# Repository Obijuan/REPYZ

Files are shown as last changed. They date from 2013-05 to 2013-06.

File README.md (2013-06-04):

REPYZ
=====

3D Printable modules for building modular robots

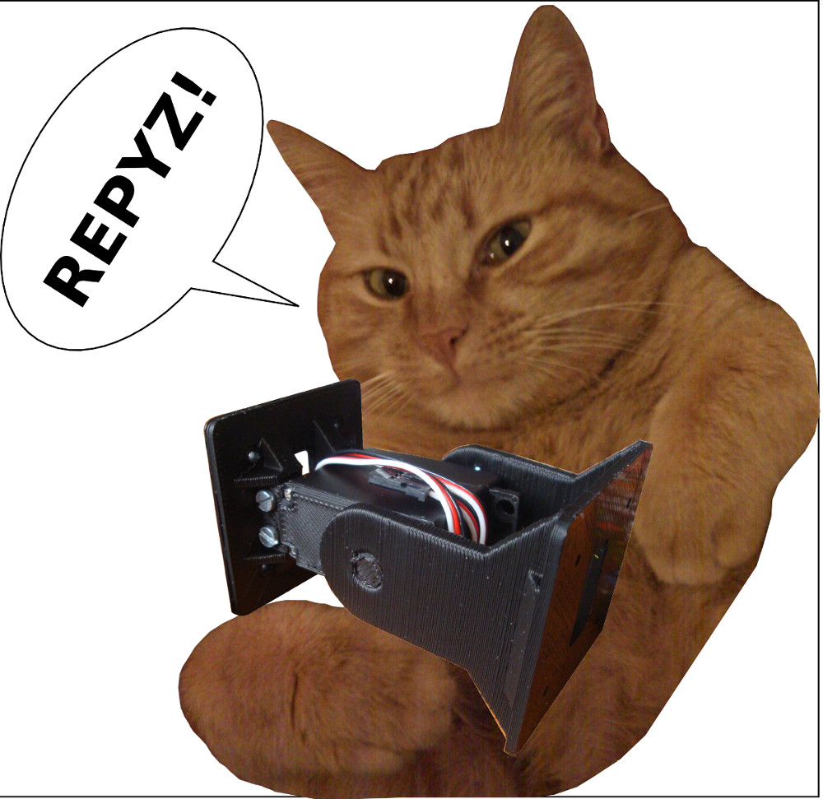
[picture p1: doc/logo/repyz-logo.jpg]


Introduction
--
REPYZ modules are an evolution of the REPY modules. The new fetures are:

- Simplified structure.  The body is smaller than in previous versions, thanks to the new sevo lower cover, with a fake shaft

- More robust and compact

- It is simmetric (like REPY v2). The caterpillar robots can move face up or face down

- PRO Version. There are two flavors of repyz modules: standar and PRO. The later includes a 608 bearing on the fake shaft for making the rotation very smooth and with no clearance.

More information can be found on this link (in Spanish):

http://www.iearobotics.com/wiki/index.php?title=M%C3%B3dulos_REPYZ

Pictures
--

https://plus.google.com/u/0/photos/109138697406392447933/albums/5878857037837654529

Video
--

  An example of the locomotion of a pith-pitch minimal configuration, composed of two repyz modules (standar version). Video presented by my little daughter Alicia :-)

http://www.youtube.com/watch?v=hIY0V6fK7iY

Bill of materials
--

- The 3 printed parts: body, head and servo lower cover (There are two differents heads, one for the standard and the other for the PRO)

- Servo Futaba 3003
- 1 M8 washer
- 1 608 bearing (optional, only for the pro version)
- 4 M3 nuts
- 4 M3x10mm bolts
- 2 M2x12mm bolts (provided with the servo)

Instructions
--



Assembly process:

https://plus.google.com/u/0/photos/109138697406392447933/albums/5884847018420290209

Electronics
--

  For moving the module all types of electronics can be used. The only requirement is the generation of a PWM signal.

  Examples of electronics:

- Arduino
- Skymega board: http://www.thingiverse.com/thing:14197
   -This is the board I am using because it fits perfectly on the REPYZ module
   
Software
--

  For generating the locomotion of snake robots, I am using sinusoidal generators. More information can be found on my phd dissertation:

http://www.iearobotics.com/wiki/index.php?title=Juan_Gonzalez:PhD_Thesis

   I have implemented the ardusnake library (for arduino and arudino compatible boards). It is very simple to use and understand:

  https://github.com/Obijuan/ArduSnake

  http://www.thingiverse.com/thing:21401

Links to other modules
--

- **Y1 modules**: http://www.iearobotics.com/wiki/index.php?title=M%C3%B3dulos_Y1
- **MY1 modules**: http://www.iearobotics.com/wiki/index.php?title=M%C3%B3dulos_MY
- **REPY v1**: http://www.thingiverse.com/thing:688
- **REPY v1.1**: http://www.thingiverse.com/thing:13442
- **REPY v2**: http://www.dsquaredrobotics.com/wiki/index.php?title=REPY-2.0

Author
--

- Juan Gonzalez-Gomez (Obijuan)

Credits
--

- **David Estevez**:  Is the author of the Repy modules v2. Repyz were inspired in Repy v2:
    http://www.dsquaredrobotics.com/wiki/index.php?title=REPY-2.0

- **Andres Prieto-Moreno**. Is the author of the MY1 modules, in which the repyz are also inspired. He also suggested me the idea of including a lower servo cover with ears for the servos. Because of these ears, the body of the module has been dramatically simplified.

- **Gocha** is the cat of Carlos Garcia Saura. It is the one that appears on the REPYZ logo

License
--

REPYZ modules are released under the GPL license

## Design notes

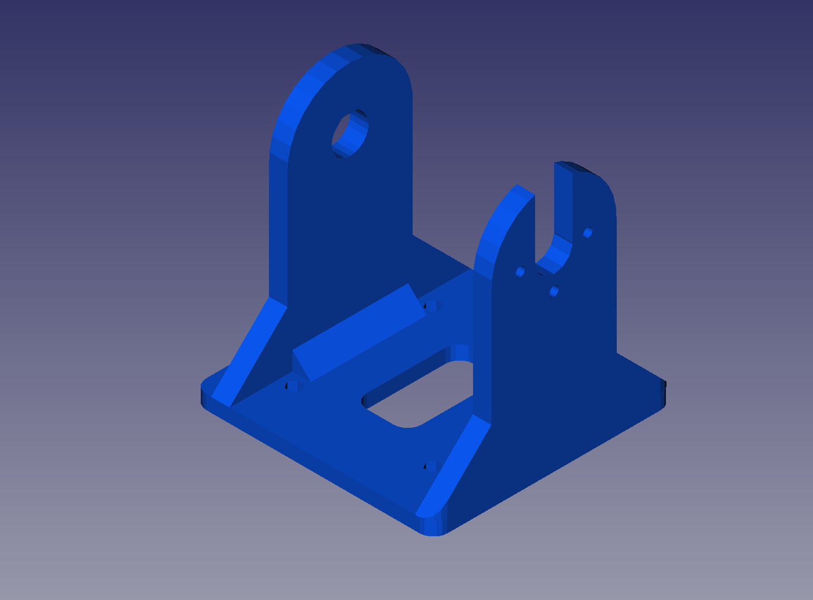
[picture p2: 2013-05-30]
pictures/REPYZ-head.png

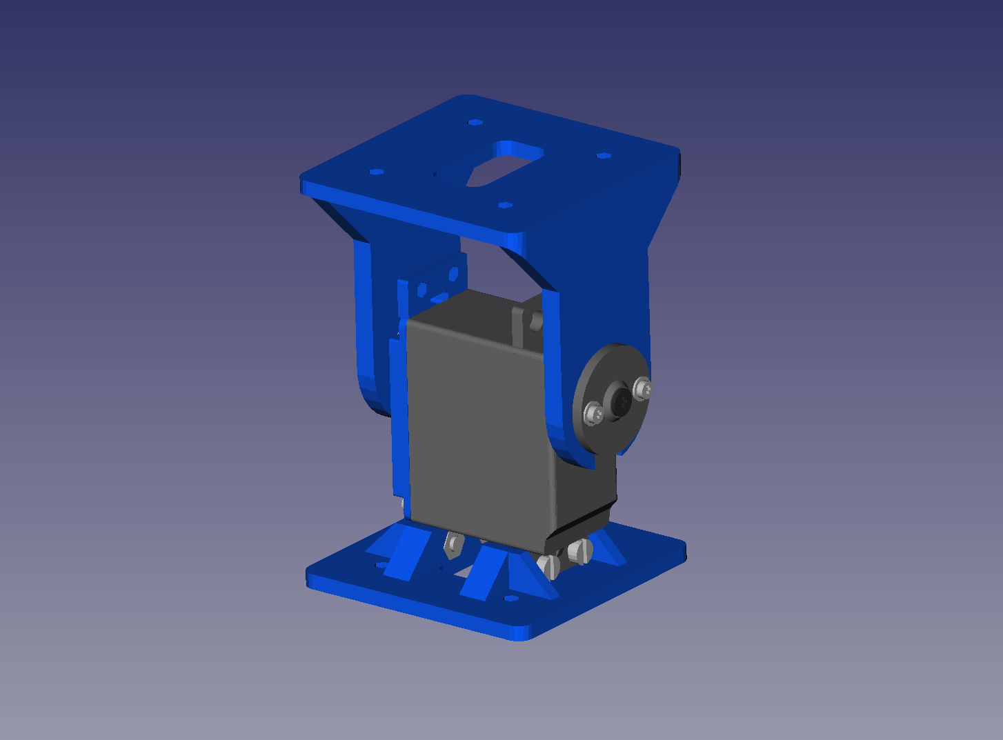
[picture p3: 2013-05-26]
pictures/repyz-module-freecad-1.png

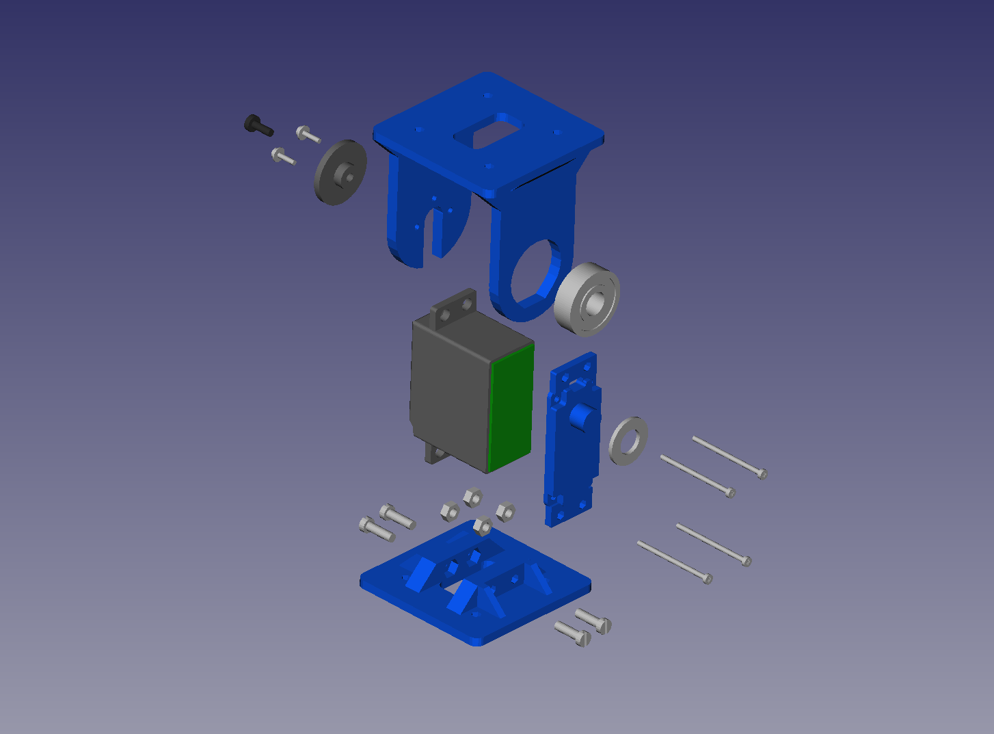
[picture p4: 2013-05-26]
pictures/repyz-PRO-module-exploded-view.png

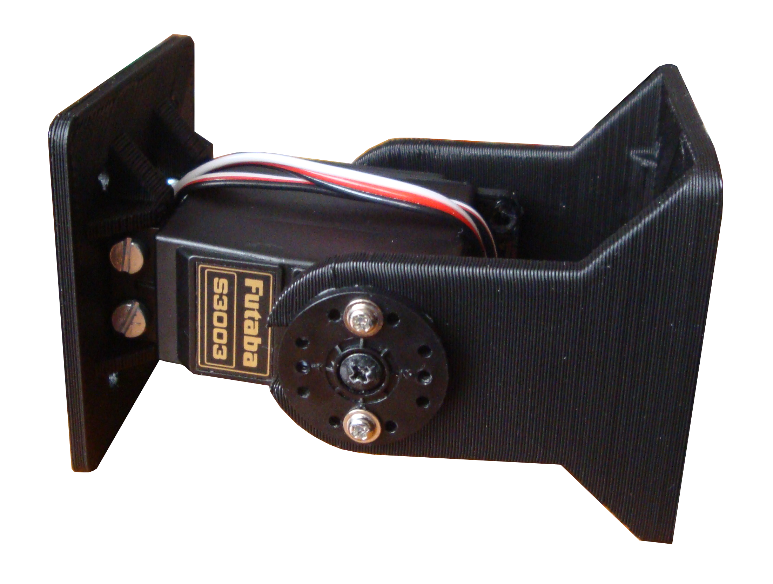
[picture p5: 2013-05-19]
pictures/REPYZ-2.png

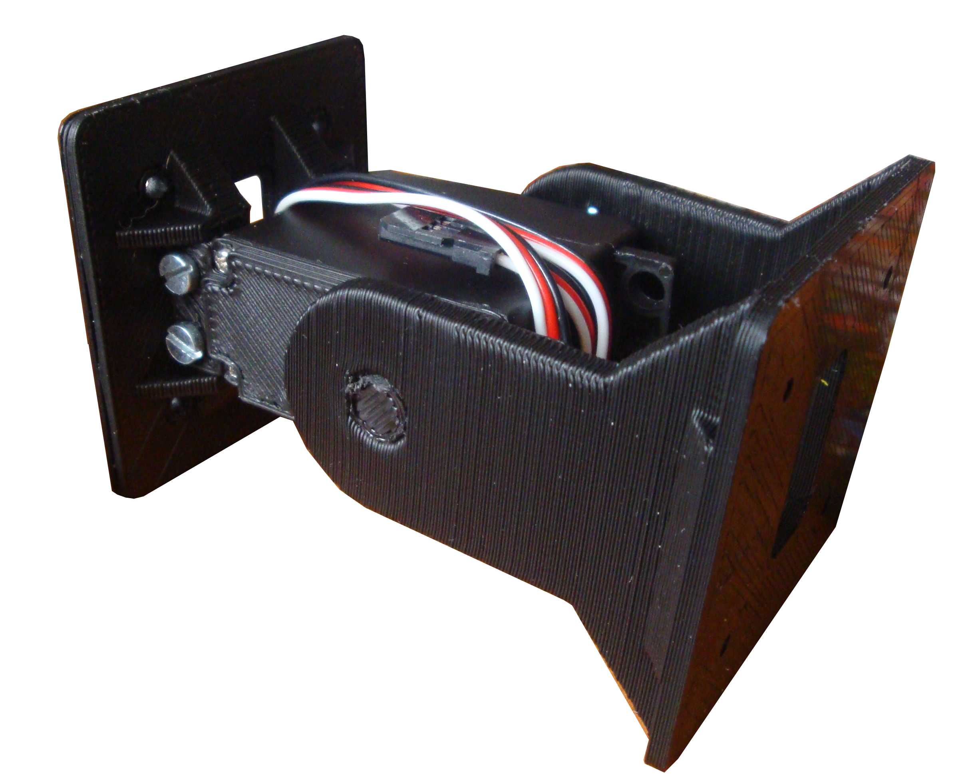
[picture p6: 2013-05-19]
pictures/REPYZ-1.png

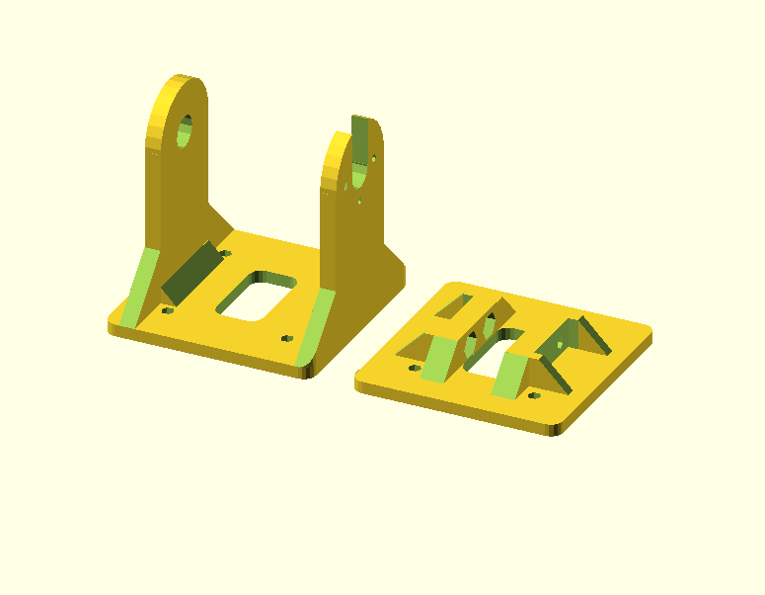
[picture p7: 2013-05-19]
pictures/repyz-body-head-openscad1.png

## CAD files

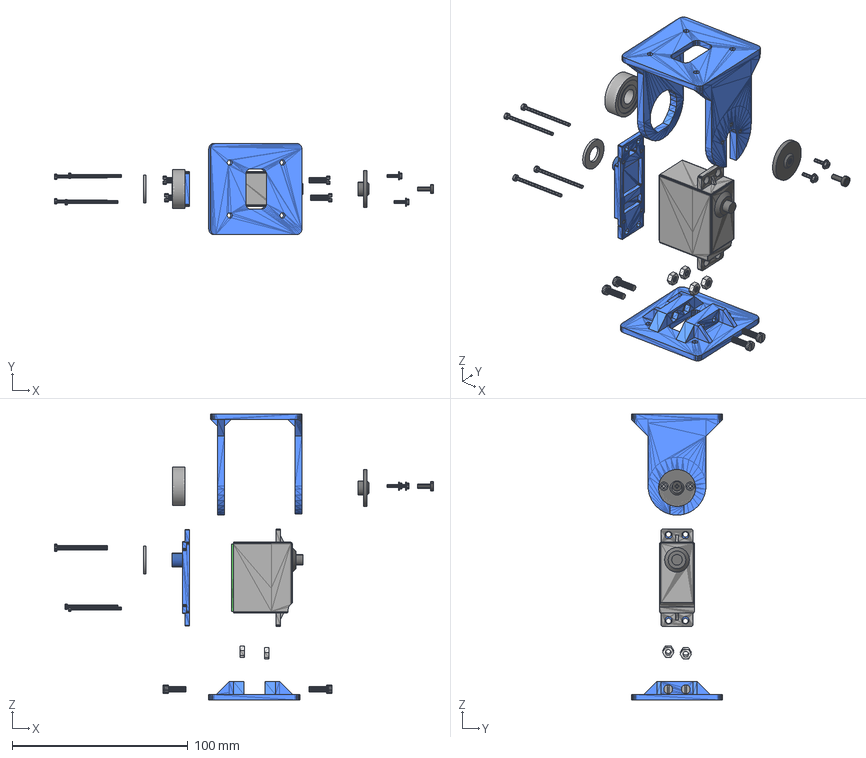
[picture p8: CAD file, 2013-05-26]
doc/Freecad/repyz-PRO-exploded-view.fcstd
215.5 x 52.0 x 162.5 mm
futaba_witout_lower_cover001
futaba_fake_electronics001
servo_lower_cover_ears_shaft001
servo_screw001
servo_screw004
servo_screw005
servo_screw006
repyz-body
nut_M3001
nut_M3004
nut_M3005
nut_M3006
bolt_M3x10_1
bolt_M3x10004
bolt_M3x10005
bolt_M3x10006
washer_M8001
futaba_rounded_horn001
servo_screw2003
servo_screw2004
servo_shaft_screw001
repyz_head_PRO001
bearing_608

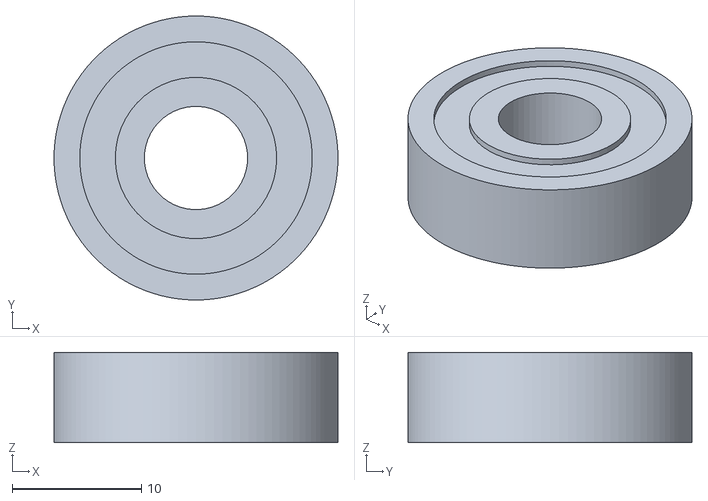
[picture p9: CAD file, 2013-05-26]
doc/Freecad/STL/608.stl
22.0 x 22.0 x 7.00

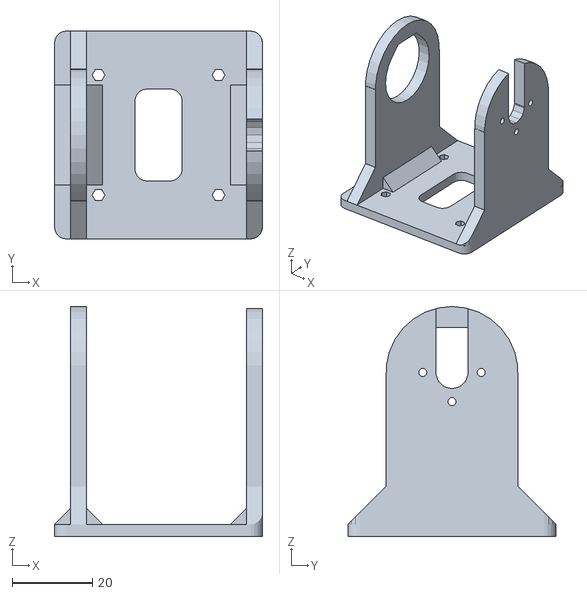
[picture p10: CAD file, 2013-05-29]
STL/repyz-head-PRO.stl
52.0 x 52.0 x 57.5

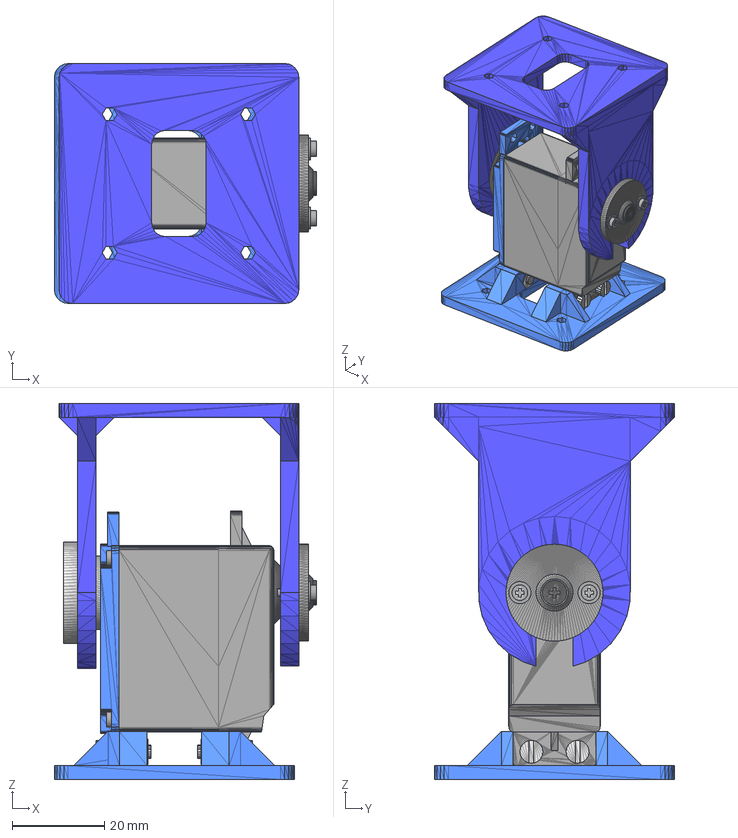
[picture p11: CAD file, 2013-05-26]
doc/Freecad/repyz-PRO.fcstd
56.8 x 52.0 x 81.5 mm
futaba_witout_lower_cover001
futaba_fake_electronics001
servo_lower_cover_ears_shaft001
servo_screw001
servo_screw004
servo_screw005
servo_screw006
repyz-body
nut_M3001
nut_M3004
nut_M3005
nut_M3006
bolt_M3x10_1
bolt_M3x10004
bolt_M3x10005
bolt_M3x10006
washer_M8001
futaba_rounded_horn001
servo_screw2003
servo_screw2004
servo_shaft_screw001
repyz_head_PRO001
bearing_608

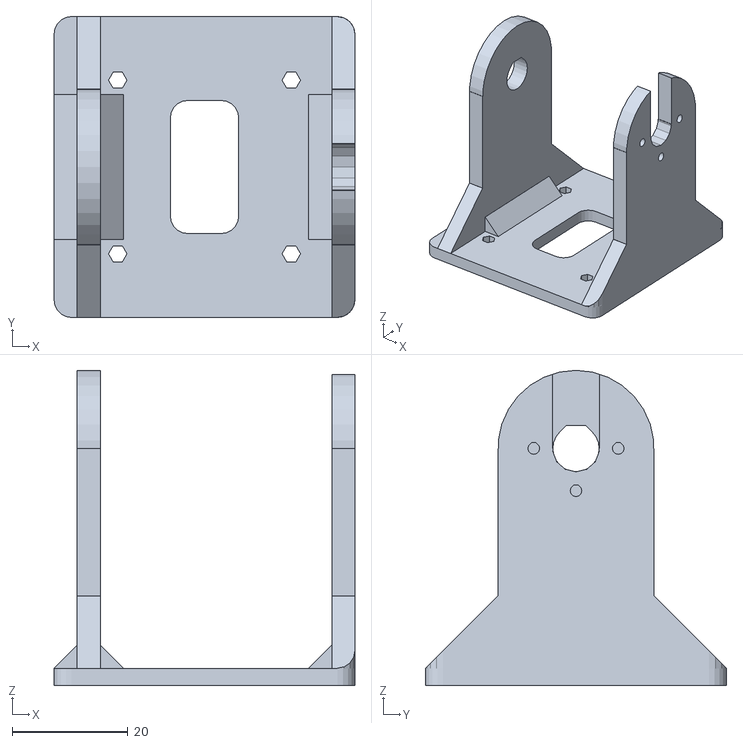
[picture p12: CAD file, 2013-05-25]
STL/repyz-head.stl
52.0 x 52.0 x 54.5

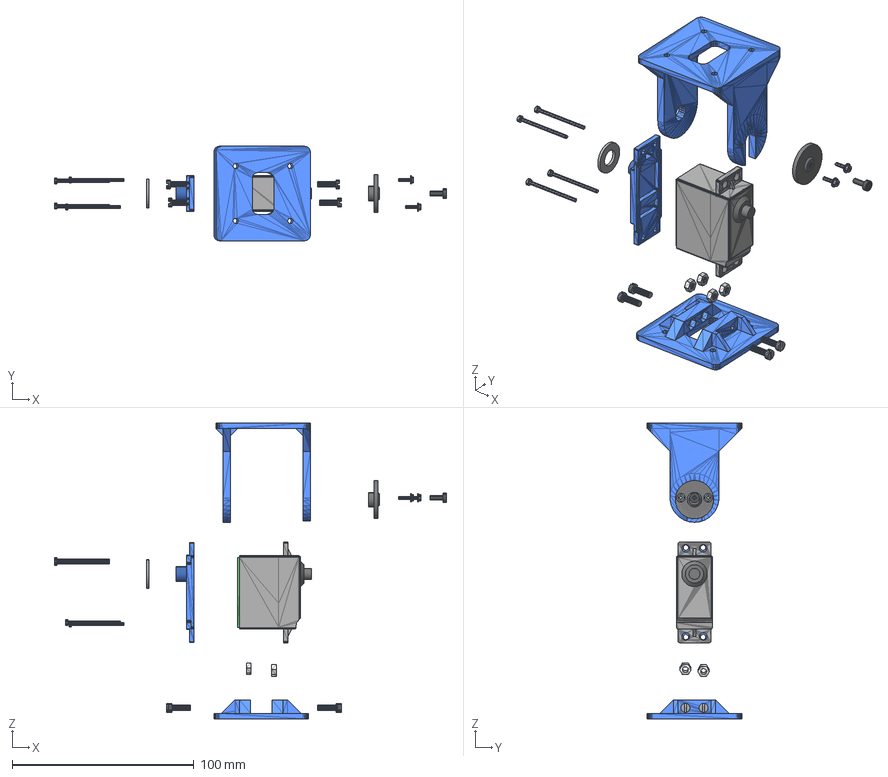
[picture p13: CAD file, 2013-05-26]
doc/Freecad/repyz-exploded-view.fcstd
215.5 x 52.0 x 162.5 mm
futaba_witout_lower_cover001
futaba_fake_electronics001
servo_lower_cover_ears_shaft001
servo_screw001
servo_screw004
servo_screw005
servo_screw006
repyz-body
nut_M3001
nut_M3004
nut_M3005
nut_M3006
bolt_M3x10_1
bolt_M3x10004
bolt_M3x10005
bolt_M3x10006
repyz_head001
washer_M8001
futaba_rounded_horn001
servo_screw2003
servo_screw2004
servo_shaft_screw001

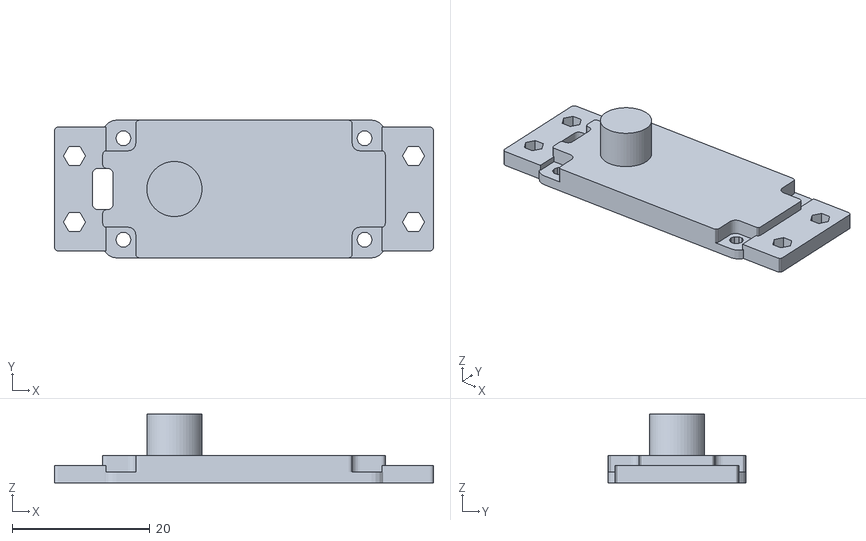
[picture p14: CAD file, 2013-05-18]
STL/servo_lower_cover_fake_shaft.stl
55.0 x 20.0 x 10.0

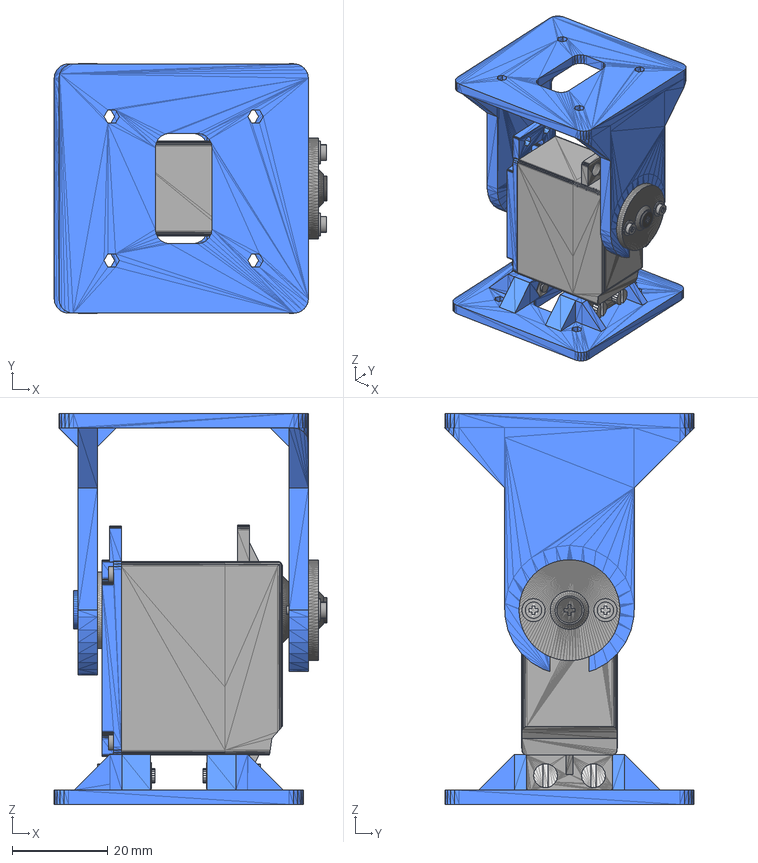
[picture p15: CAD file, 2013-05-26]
doc/Freecad/repyz.fcstd
56.8 x 52.0 x 81.5 mm
futaba_witout_lower_cover001
futaba_fake_electronics001
servo_lower_cover_ears_shaft001
servo_screw001
servo_screw004
servo_screw005
servo_screw006
repyz-body
nut_M3001
nut_M3004
nut_M3005
nut_M3006
bolt_M3x10_1
bolt_M3x10004
bolt_M3x10005
bolt_M3x10006
repyz_head001
washer_M8001
futaba_rounded_horn001
servo_screw2003
servo_screw2004
servo_shaft_screw001

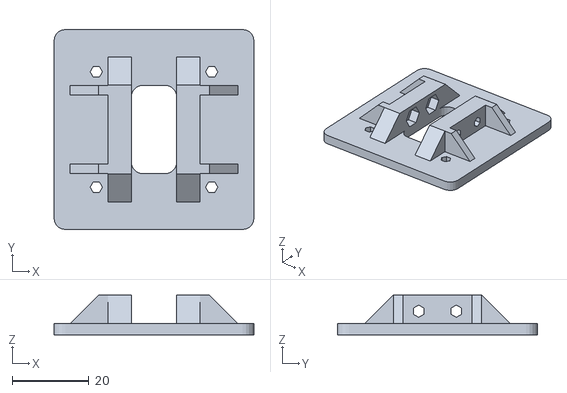
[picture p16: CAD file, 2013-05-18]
STL/repyz-body.stl
52.0 x 52.0 x 10.4

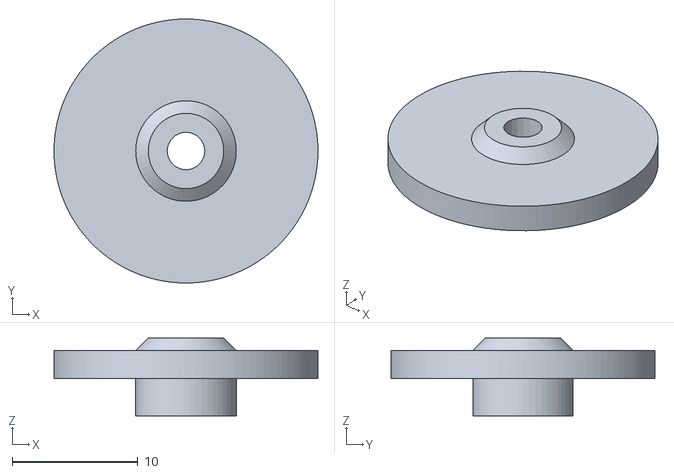
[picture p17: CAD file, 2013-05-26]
doc/Freecad/STL/futaba_rounded_horn.stl
21.0 x 21.0 x 6.20

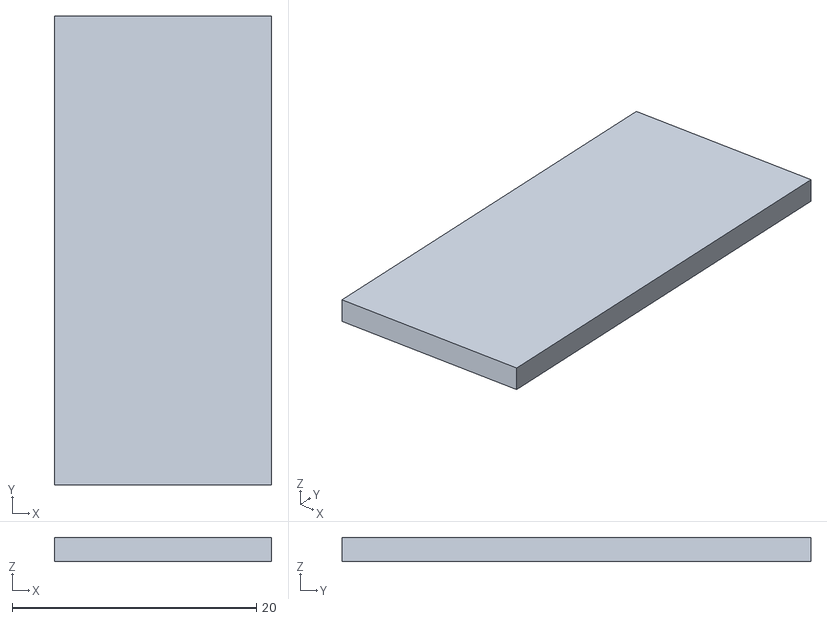
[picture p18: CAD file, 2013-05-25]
doc/Freecad/STL/futaba_fake_electronics.stl
17.8 x 38.4 x 2.00

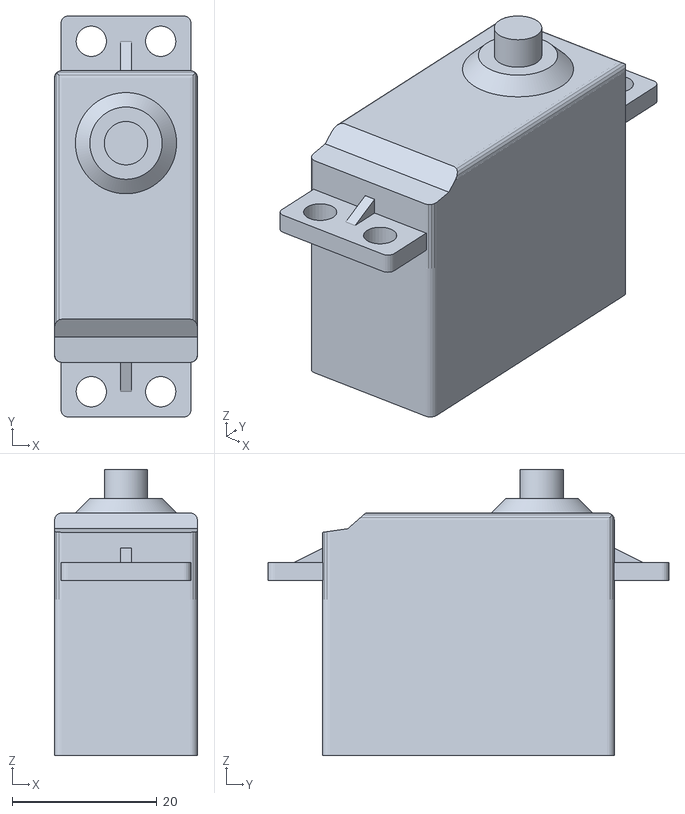
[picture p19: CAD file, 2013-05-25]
doc/Freecad/STL/futaba_witout_lower_cover.stl
19.8 x 55.5 x 39.6

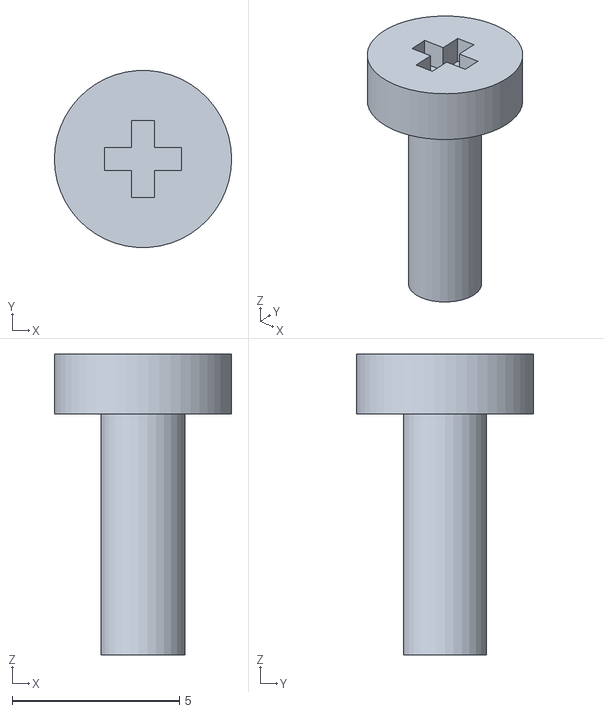
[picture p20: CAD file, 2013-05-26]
doc/Freecad/STL/servo_shaft_screw.stl
5.30 x 5.29 x 9.00

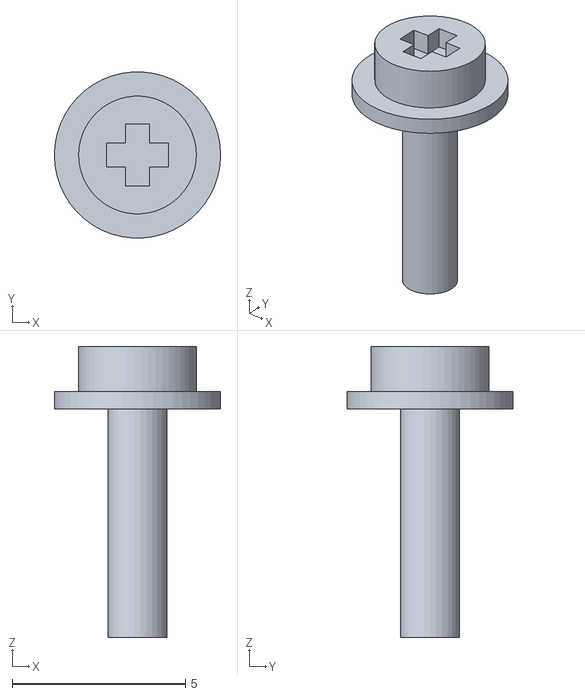
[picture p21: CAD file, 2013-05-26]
doc/Freecad/STL/servo_screw2.stl
4.80 x 4.79 x 8.40

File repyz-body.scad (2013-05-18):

use <obiscad/bcube.scad>
use <obiscad/bevel.scad>
use <obiscad/attach.scad>

X = 0;
Y = 1;
Z = 2;

//----------------- USER parameters ------------------
base_side = 52;
base_th = 3;
base_cr = 3;
base_cres = 4;

ear_lx = 23.8;
ear_lz = 7.4;

ear_size = [2.5, 18, 7.4];
ear_pos_h = 1.5;

foot_th = 6;
foot_size = [foot_th + ear_size[X], 23, ear_lz];

foot_drill_diam = 3.2;
foot_drill_h = 1.6;

//-- Distance between the center of the two
//-- foot drills
foot_drill_dx = 6.6 + foot_drill_diam;

//---------------------- DATA calculation
base_size = [base_side, base_side, base_th];

//-- Distance in x between the two feet
feet_dx = ear_lx - 2 * foot_th;

//-- Feet location coordinates
foot_pos = [foot_size[X]/2 + feet_dx/2,
            0,
            foot_size[Z]/2 + base_size[Z]/2 - 0.01];

            //foot_pos[X] - foot_size[X]
//-- Steps----
step1_size = [2.5, foot_size[Y], 1.5];
step1_pos = [-step1_size[X]/2 - foot_pos[X] - foot_size[X]/2,
            0,
            step1_size[Z]/2 + base_size[Z]/2];
            
//-- captive Nuts
nut_h = 3;
nut_radius = 6.6/2;            
            
extra = 5;


//--- SKYMEGA Drills
sky_dd = 15;  //-- Distance

sky_drill_table = [
  [sky_dd, sky_dd, 0],
  [-sky_dd, sky_dd, 0],
  [-sky_dd, -sky_dd, 0],
  [sky_dd, -sky_dd, 0],
];

sky_drill_diam = 3.2;


//--- Center cutouts
co1_size = [feet_dx, foot_size[Y], base_size[Z]+extra];

//-- Feet reinforment (in x direction)
//-- Define the connectors

//-- Reinforments x-direction thickness
rx_th = (foot_size[Y]-ear_size[Y])/2;
rx_pos = [-foot_size[X]/2, ear_size[Y]/2 + rx_th/2, -foot_size[Z]/2];

rx_ec1 = [ [rx_pos[X], rx_pos[Y], rx_pos[Z]], [0,1,0], 0];
rx_en1 = [ rx_ec1[0], [-1,0,1], 0];

rx_ec2 = [ [rx_pos[X], -rx_pos[Y], rx_pos[Z]], [0,-1,0], 0];
rx_en2 = [ rx_ec2[0], [-1,0,1], 0];


//-- Reinforments in the y direction
ry_th = foot_size[X] - ear_size[X];
ry_pos = [ear_size[X]/2, foot_size[Y]/2, -foot_size[Z]/2];

ry_ec1 = [ [ry_pos[X], ry_pos[Y], ry_pos[Z]], [-1,0,0], 0];
ry_en1 = [ ry_ec1[0], [0,1,1], 0];

ry_ec2 = [ [ry_pos[X], -ry_pos[Y], ry_pos[Z]], [1,0,0], 0];
ry_en2 = [ ry_ec2[0], [0,-1,1], 0];


//-- For debuging
*connector(rx_ec1);
*connector(rx_en1);
*connector(ry_ec4);
*connector(ry_en4);


module foot()
{

  nut_co = nut_h + extra;
  
  ear_co_size = [ear_size[X]+extra, ear_size[Y], ear_size[Z]+extra];
  foot_drill_pos = [0, 
               foot_drill_dx/2, 
               -foot_size[Z]/2 + foot_drill_diam/2 + foot_drill_h];

  union() {
  
    //-- Foot
    difference() {
      //-- Main foot body
      cube(foot_size, center = true);
    
      //-- space for the servo ear
      translate([-ear_co_size[X]/2 - foot_size[X]/2 + ear_size[X],
		0,
		0])
      cube(ear_co_size, center = true);
      
      //-- Foot drills
      translate(foot_drill_pos)
      rotate([0, 90, 0])
      cylinder(r = foot_drill_diam/2, h = foot_size[X] + extra, center = true);

      translate([foot_drill_pos[X], -foot_drill_pos[Y], foot_drill_pos[Z]])
      rotate([0, 90, 0])
      cylinder(r = foot_drill_diam/2, h = foot_size[X] + extra, center = true);
      
      //-- Embebed nuts
      translate([nut_co/2 + foot_size[X]/2 - nut_h,
		foot_drill_dx/2,
		  foot_drill_pos[Z]])
      rotate([0,90,0])
      rotate([0,0,90])
      cylinder(r = nut_radius, h = nut_co, center = true, $fn=6);
  
      translate([nut_co/2 + foot_size[X]/2 - nut_h,
		-foot_drill_dx/2,
		  foot_drill_pos[Z]])
      rotate([0,90,0])
      rotate([0,0,90])
      cylinder(r = nut_radius, h = nut_co, center = true, $fn=6);
      
    }
  
    //-- X-reinforments
    bconcave_corner_attach(rx_ec1, rx_en1, l=rx_th, cr=foot_size[Z], cres=0, th=0.1);
    bconcave_corner_attach(rx_ec2, rx_en2, l=rx_th, cr=foot_size[Z], cres=0, th=0.1);

    //-- Y-reinforments
    bconcave_corner_attach(ry_ec1, ry_en1, l=ry_th, cr=foot_size[Z], cres=0, th=0.1);
    bconcave_corner_attach(ry_ec2, ry_en2, l=ry_th, cr=foot_size[Z], cres=0, th=0.1);
  
  }

}
 
*foot(); 


 
//--------- PART building -----------------
difference() {
  //-- The base
  bcube(base_size, cr = base_cr, cres = base_cres);
  
  //-- Skymega drills
  for (drill = sky_drill_table) {
    translate(drill)
      cylinder(r=sky_drill_diam/2, h=base_size[Z]+extra,center=true, $fn=6);
  }
  
  //-- Central cutout
  bcube(co1_size, cr = base_cr, cres = base_cres);

}  
  
//-- The feet

//-- Right foot
//color("blue")
translate(foot_pos)
rotate([0,0,180])
foot();

//-- Left foot
//color("blue")
translate([-foot_pos[X], foot_pos[Y], foot_pos[Z]])
foot();


//--- Things TODO
//-- * (optional) more cutouts

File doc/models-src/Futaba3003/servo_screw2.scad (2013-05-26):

X = 0;
Y = 1;
Z = 2;


len = 7.2;
diam = 1.7;

head_diam = 3.4;
head_th = 1.3;

head2_diam = 4.8;
head2_th = 0.5;

extra = 5;

cross_size = [1.8, 0.7, extra];

module cross()
{
  cube(cross_size, center = true);

  rotate([0,0,90])
    cube(cross_size, center = true);
}

module head()
{

  difference() {
    cylinder(r=head_diam/2, h = head_th, center = true, $fn=50);
    
    translate([0,0, cross_size[Z]/2])
      cross();
 }     
 
 translate([0,0, -head2_th/2 - head_th/2])
 cylinder(r=4.8/2, h = 0.5, center = true, $fn=50);

}


cylinder(r=diam/2, h = len, center = true, $fn=30);
translate([0,0,head_th/2 + len/2 -0.1])
head();

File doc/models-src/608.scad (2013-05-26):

diam = 22;
idiam = 8;
th = 7;

extra = 10;

module ring(id, od, th)
{
  difference() {
    cylinder(r = od/2, h = th, center = true, $fn = 100);
    cylinder(r = id/2, h = th + extra, center = true, $fn = 50);
  }
}

difference() {
  ring (id = idiam, od = diam, th = th);

  translate([0,0,3/2 + th/2 -0.5])
    ring(id = 12.5, od = 18, th = 3);

  translate([0,0, -3/2 - th/2 +0.5])
    ring(id = 12.5, od = 18, th = 3);
}

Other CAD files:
doc/Freecad/STL/washer_M8.stl
doc/Freecad/STL/bolt_M3x10.stl
doc/Freecad/STL/nut_M3.stl
doc/Freecad/STL/servo_screw.stl
doc/models-src/Futaba3003/servo_shaft_screw.scad
doc/models-src/Futaba3003/futaba.scad
doc/models-src/Futaba3003/futaba_rounded_horn.scad
doc/models-src/Futaba3003/obiscad/attach.scad
doc/models-src/Futaba3003/obiscad/bcube.scad
doc/models-src/Futaba3003/obiscad/bevel.scad
doc/models-src/Futaba3003/obiscad/utils.scad
doc/models-src/Futaba3003/obiscad/vector.scad
doc/models-src/Futaba3003/servo_screw.scad
doc/models-src/bolt.scad
doc/models-src/nut.scad
doc/models-src/washer.scad
openscad/main.scad
openscad/servo_lower_cover.scad
openscad/teardrop.scad

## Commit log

2013-05-17 Base + early feet for testing
    [repyz-body.scad]
2013-05-17 First test. TODO added
    [repyz-body.scad]
2013-05-17 Skymega drills, central cutout and the left step added
    [repyz-body.scad]
2013-05-17 Space for the servo ears in the feet
    [repyz-body.scad]
2013-05-18 Release candidate 1
    [repyz-body.scad]
2013-05-18 Bug Fixed. Error when slicing with slic3r
    [repyz-body.scad]
2013-05-18 New openscad module for repyz_body. Sources moved to openscad folder
    [attach.scad, bcube.scad, bevel.scad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]
2013-05-18 Servo lower cover added
    [servo_lower_cover.scad]
2013-05-18 STL files for the servo lower cover and repyz body
    [repyz-body.stl, servo_lower_cover_fake_shaft.stl]
2013-05-18 First draft of the repyz-head (bearing-less)
    [repyz-body.scad]
2013-05-18 Reinforments added. Release candidate 1
    [repyz-body.scad]
2013-05-18 File renamed to main.scad. The body and head are in this file
    [main.scad]
2013-05-19 Code cleaned and documented
    [main.scad]
2013-05-19 STL for the module's head
    [repyz-head.stl]
2013-05-19 Standar module head is longer on the y-axis. First draft of the PRO version
    [main.scad, repyz-head.stl]
2013-05-19 Version PRO (with 608 bearing) tested. It should be improved, but it is working
    [repyz-head-PRO.stl]
2013-05-19 TODO updated
    [main.scad]
2013-05-25 Vertical drills changed to teardrops instead of cylinders
    [main.scad, teardrop.scad]
2013-05-25 STLs with teardrops drills
    [main.scad, repyz-head-PRO.stl, repyz-head.stl]
2013-05-25 Freecad diagram: first draft
    [attach.scad, bcube.scad, bevel.scad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]
2013-05-25 Some vitamins for the Freecad drawing
    [bolt.scad, bolt_M3x10.stl, main.scad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]
2013-05-26 repyz head added to the freecad drawing
    [repyz.fcstd]
2013-05-26 Servo horn screws modelled
    [servo_screw2.stl]
2013-05-26 M8 washer added
    [futaba_rounded_horn.scad, futaba_rounded_horn.stl, repyz.fcstd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]
2013-05-26 Screws for attaching the servo horn to the repyz head added
    [repyz.fcstd, servo_screw2.scad, servo_screw2.stl]
2013-05-26 Servo shaft screw added. Freecad drawing ready
    [repyz.fcstd, servo_shaft_screw.scad, servo_shaft_screw.stl]
2013-05-26 Pictures (Freecad) of the module assembled
    [repyz.fcstd]
2013-05-26 Repyz module exploded view (Freecad)
    [repyz-exploded-view.fcstd]
2013-05-26 Freecad drawing of the repyz-PRO
    [608.scad, 608.stl, repyz-PRO.fcstd]
2013-05-26 Repyz PRO: exploded drawing (Freecad)
    [repyz-PRO-exploded-view.fcstd]
2013-05-29 Images of body and servo lower cover parts added
2013-05-29 Repyz-pro: bearing hole diameter bigger: +0.5mm
    [main.scad, repyz-head-PRO.stl]
2013-06-02 Arduino firmware for moving to REPYZ to its home position (needed when assembling)
